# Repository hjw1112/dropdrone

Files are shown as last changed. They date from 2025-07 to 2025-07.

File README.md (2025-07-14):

# Dropdrone

This is a custom 5 inch fpv drone with modular payload system that is designed to drop stuff. (NOT for dangerous things and I will use this only in my backyard or open field in low height)

I built this because i wanted to try to move things with drone after watching some fpv drones with payload system on youtube. Also, I wanted to experience to build a fpv drone by myself not buying prebuilt stuff.

you can reference this project + copy/modify. All source files are in this repo.

### 3D model of the payload module

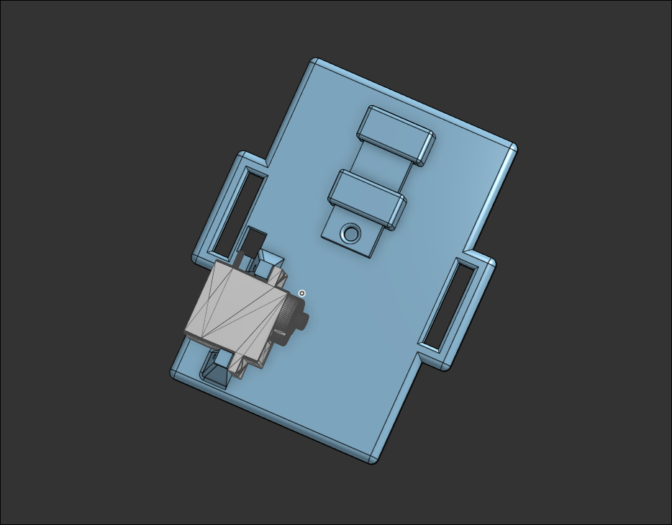
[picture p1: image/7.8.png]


### 3D model of frame

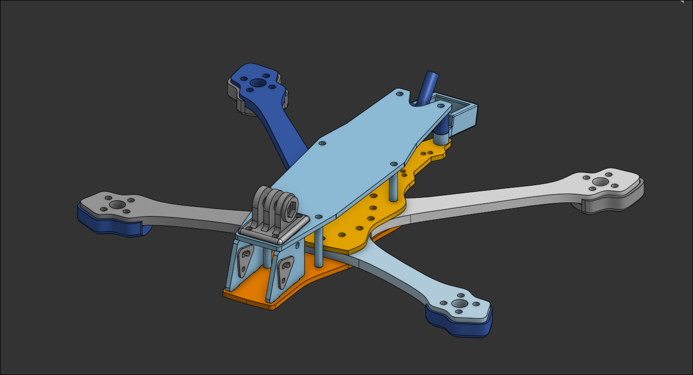
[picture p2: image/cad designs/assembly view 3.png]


### Onshape document
https://cad.onshape.com/documents/2c66b1014f978a30ab8967e0/w/781099a0622bf4fd1c422891/e/69bb565c8f452c8e317ebf30

### BOM

| Component | Price | Source | Link |
|---|---|---|---|
| GPS | $16.56  | aliexpress | [Link](https://www.aliexpress.com/item/1005008590174242.html?spm=a2g0o.cart.0.0.583438dalVaNCs&mp=1) |
| standoff 25mm, 18mm | $5.51 | aliexpress | [Link](https://www.aliexpress.com/item/10050003175594672.html?spm=a2g0o.cart.0.0.583438dalVaNCs&mp=1) |
| motor | $35.15  | aliexpress | [Link](https://www.aliexpress.com/item/1005005247800911.html?spm=a2g0o.cart.0.0.583438dalVaNCs&mp=1) |
| xt60 connector | $1.20 | aliexpress | [Link](https://www.aliexpress.com/item/1005007103483786.html?spm=a2g0o.cart.0.0.583438dalVaNCs&mp=1) |
| mipi cable for air unit| $4.15 | aliexpress | [Link](https://www.aliexpress.com/item/1005009341460132.html?spm=a2g0o.cart.0.0.583438dalVaNCs&mp=1) |
| m3 and m5 wrench | $3.54 | aliexpress | [Link](https://www.aliexpress.com/item/4000116377065.html?spm=a2g0o.cart.0.0.583438dalVaNCs&mp=1) |
| non-slip pad for battery| $3.46  | aliexpress | [Link](https://www.aliexpress.com/item/1005009871344968.html?spm=a2g0o.cart.0.0.583438dalVaNCs&mp=1) |
| m3 screw set | $8.43 | aliexpress | [Link](https://www.aliexpress.com/item/1005004526857141.html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) |
| battery strap | $2.75 | aliexpress | [Link](https://www.aliexpress.com/item/1005005249789396.html?spm=a2g0o.cart.0.0.583438dalVaNCs&mp=1) |
| lipo charger | $29.04  | aliexpress | [Link](https://www.aliexpress.com/item/1005003623858420.html?spm=a2g0o.cart.0.0.583438dalVaNCs&mp=1) |
| sg90 servo | $1.96 | aliexpress | [Link](https://www.aliexpress.com/item/1005000625304079.html?spm=a2g0o.cart.0.0.583438dalVaNCs&mp=1) |
| lipo bag | $2.98 | aliexpress | [Link](https://www.aliexpress.com/item/1005005071740139.html?spm=a2g0o.cart.0.0.583438dalVaNCs&mp=1) |
| threadlock | $1.86 | aliexpress | [Link](https://www.aliexpress.com/item/1005008289081577.html?spm=a2g0o.cart.0.0.583438dalVaNCs&mp=1) |
| fc and esc stack | $47.41  | aliexpress | [Link](https://www.aliexpress.com/item/1005007001011519.html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) |
| props x2 | $7.48 | aliexpress | [Link](https://www.aliexpress.com/item/1005007433514825.html?spm=a2g0o.cart.0.0.583438dalVaNCs&mp=1) |

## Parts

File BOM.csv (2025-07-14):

Component | Price | Source | link
GPS | $16.56 | aliexpress | https://www.aliexpress.com/item/1005008590174242.html?spm=a2g0o.cart.0.0.583438daIVaNCs&mp=1
standoff 25mm, 18mm | $5.51 | aliexpress | https://www.aliexpress.com/item/1005003175594672.html?spm=a2g0o.cart.0.0.583438daIVaNCs&mp=1 https://www.aliexpress.com/item/1005003175594672.html?spm=a2g0o.cart.0.0.583438daIVaNCs&mp=1
motor | $35.15 | aliexpress | https://www.aliexpress.com/item/1005005247800911.html?spm=a2g0o.cart.0.0.583438daIVaNCs&mp=1
xt60 connector | $1.20 | aliexpress | https://www.aliexpress.com/item/1005007103438736.html?spm=a2g0o.cart.0.0.583438daIVaNCs&mp=1
mipi cable for air unit | $4.15 | aliexpress | https://www.aliexpress.com/item/1005009431460132.html?spm=a2g0o.cart.0.0.583438daIVaNCs&mp=1
m3 and m5 wrench | $3.54 | aliexpress | https://www.aliexpress.com/item/4000017637065.html?spm=a2g0o.cart.0.0.583438daIVaNCs&mp=1
non-slip pad for battery | $3.86 | aliexpress | https://www.aliexpress.com/item/1005006987134496.html?spm=a2g0o.cart.0.0.583438daIVaNCs&mp=1
m3 screw set | $8.43 | aliexpress | https://www.aliexpress.com/item/1005004526853714.html?mp=1
battery strap | $2.75 | aliexpress | https://www.aliexpress.com/item/1005007125752501.html?spm=a2g0o.cart.0.0.583438daIVaNCs&mp=1
lipo charger | $29.04 | aliexpress | https://www.aliexpress.com/item/1005005947893976.html?spm=a2g0o.cart.0.0.583438daIVaNCs&mp=1
sg90 servo | $1.96 | aliexpress | https://www.aliexpress.com/item/1005006283358420.html?spm=a2g0o.cart.0.0.583438daIVaNCs&mp=1
lipo bag | $2.98 | aliexpress | https://www.aliexpress.com/item/1005007625304079.html?spm=a2g0o.cart.0.0.583438daIVaNCs&mp=1
threadlock | $1.86 | aliexpress | https://www.aliexpress.com/item/1005008298085771.html?spm=a2g0o.cart.0.0.583438daIVaNCs&mp=1
fc and esc stack | $47.41 | aliexpress | https://www.aliexpress.com/item/1005007050011519.html?spm=a2g0o.cart.0.0.583438daIVaNCs&mp=1
props x2 | $7.48 | aliexpress | https://www.aliexpress.com/item/1005007433514825.html?mp=1
discount | $22.11
total | $149.77
I'm buying these
dji o4 air unit | $110.00 | local store
lipo battery | $50.00 | local store

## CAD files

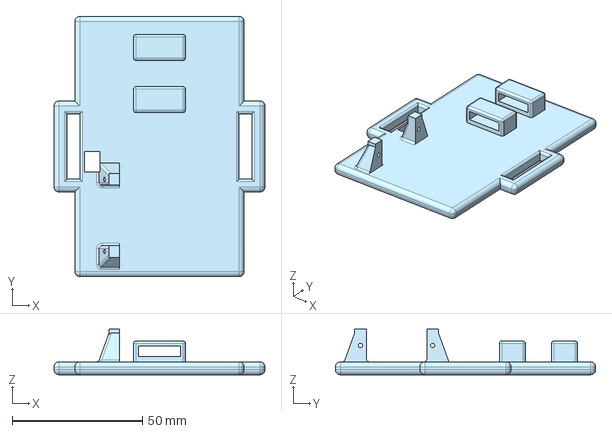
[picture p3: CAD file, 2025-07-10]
CAD/drop system/main body.step
81.0 x 100.0 x 17.5 mm

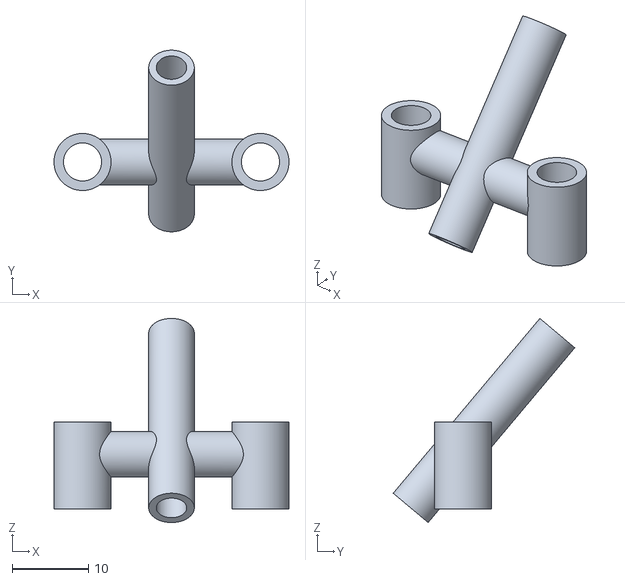
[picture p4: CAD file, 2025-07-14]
CAD/frame/antenna mount.stl
30.9 x 23.9 x 26.8

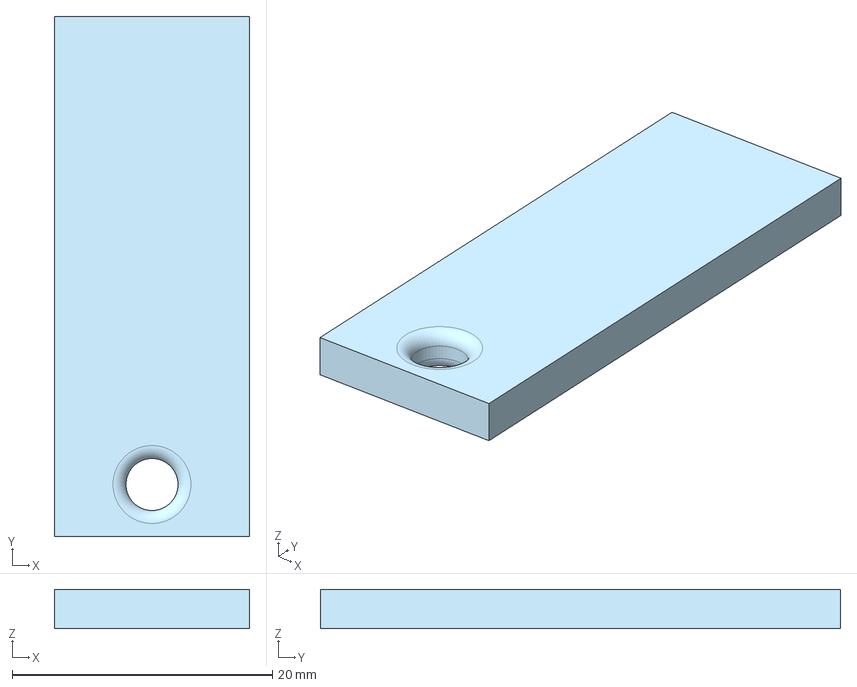
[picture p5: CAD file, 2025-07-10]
CAD/drop system/stick part.step
15.0 x 40.0 x 3.00 mm

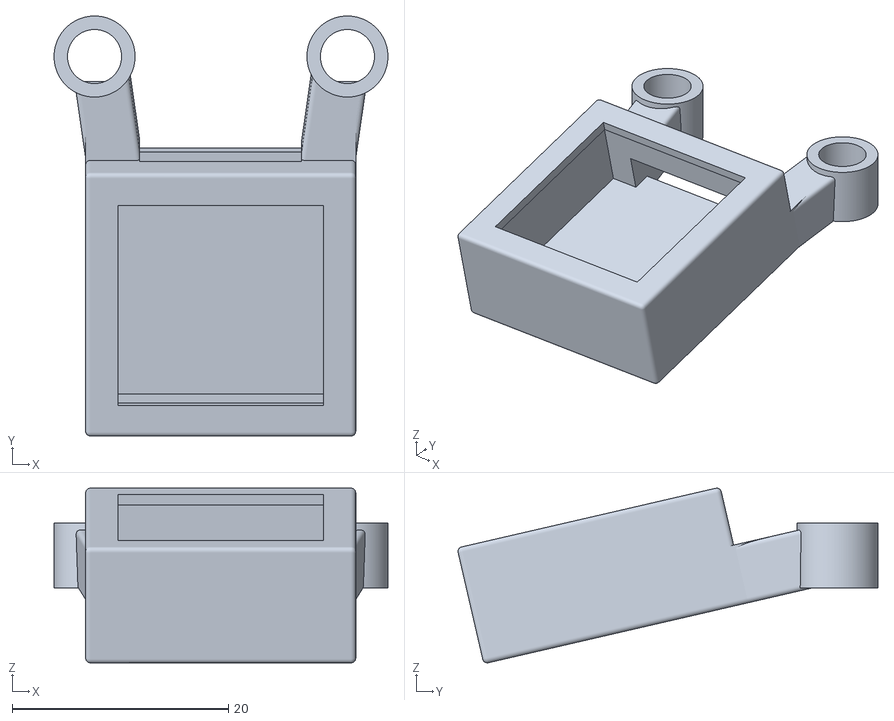
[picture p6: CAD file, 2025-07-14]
CAD/frame/gps mount.stl
30.9 x 38.9 x 16.2

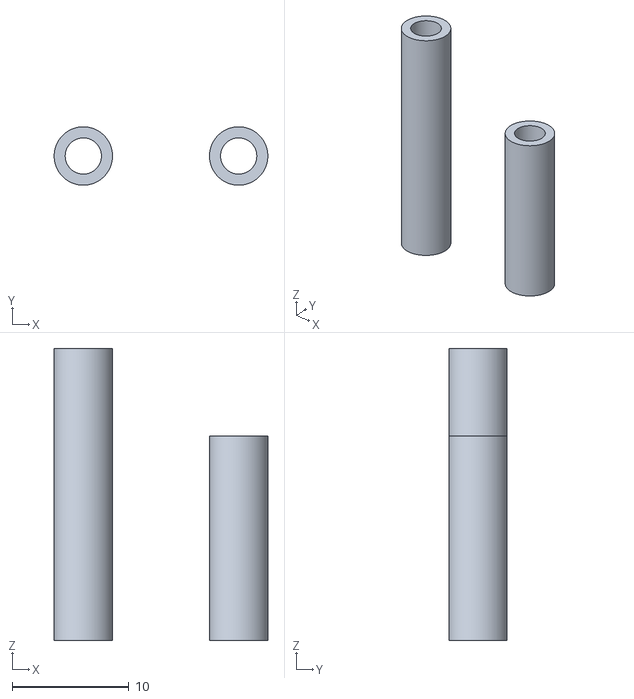
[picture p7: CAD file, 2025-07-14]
CAD/frame/standoffs.stl
18.3 x 5.00 x 25.0

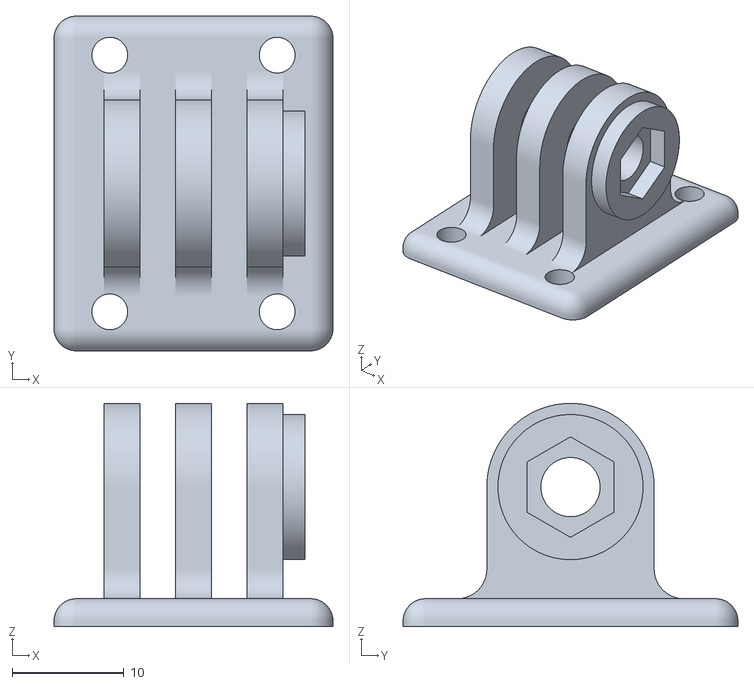
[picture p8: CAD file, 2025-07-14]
CAD/frame/gopro mount.stl
25.0 x 30.0 x 20.0

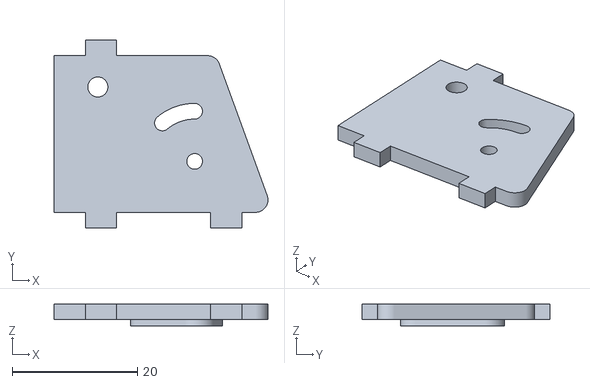
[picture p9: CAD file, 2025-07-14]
CAD/frame/side plate and cam mount.stl
34.1 x 30.0 x 3.50

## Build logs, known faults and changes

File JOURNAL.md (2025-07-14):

---
title: "Dropdrone"
author: "hjw1112"
description: "A custom built 5 inch fpv drone that can carry stuff"
created_at: "2025-07-04"
---

### onshape document
https://cad.onshape.com/documents/2c66b1014f978a30ab8967e0/w/781099a0622bf4fd1c422891/e/69bb565c8f452c8e317ebf30

### **total hours: 40.5h**

# July 4th: Start!

I did research about components and sourced some components from aliexpress. I will use dji O4 air unit, xing 2207 motor, SG90 servo, 5 inch frame, M100 GPS, and Speedybee F450 stack. It took a while because components are expensive and i was trying to reduce cost as much as possible.

Also, I started to working on 3d modeling of servo payload system. I saw a video on youtube (https://www.youtube.com/shorts/8GbMEWLD8KA) which is simple payload system on fpv drone. I will benchmark this and make similar one. But I'm going to make it better and more refined because one in the video is made out of some random metal part and zip tie. I will use 3d printed part and possibly a metal part for stronger holder for smaller thickness.

I started looking and planning 3d model by looking at carbon fiber frame that i chose on aliexpress. I think i will mount servo on the backside of the drone and put locking system at the center of the drone for stability.

**Total time spent: 6h**

# July 5th: Component changes and 3d modeling start

I did more research and a lot of searching on aliexpress for cheaper materials. I found cheaper SG90 servo so i replaced it. and i also found similar frame for better price so i replaced it too. it doesn't include 3d printed parts but i can design and print them myself ig. I replaced speedybee stack to unknown branded but cheaper stack.

I restarted to plan 3d model again cuz i changed frame and I will use holes for holding top and bottom part together to hold 3d printed servo mount(I will use longer screw) and put servo on the mount. 

**Total time spent: 5h**

# July 6th: more component changes and 3d modeling again

I'm currently trying to reduce cost and it is so hard :(( Its 383$ now including dji O4 air unit lite. I'm trying to fit everything under 150$ without air unit and battery. I changed motor to sunfun 2207 1750kv which is cheaper.

I restarted 3d modeling AGAIN because i wanted the payload system be removable and modular since flight time can be extended if payload system is removable.
I'm planning to use fpv battery strap to hold 3d printed payload system onto the frame.

Currently, I made hole for wire and mount for servo motor. I'm planning to add strap hole on the left and right side.

### Current CAD

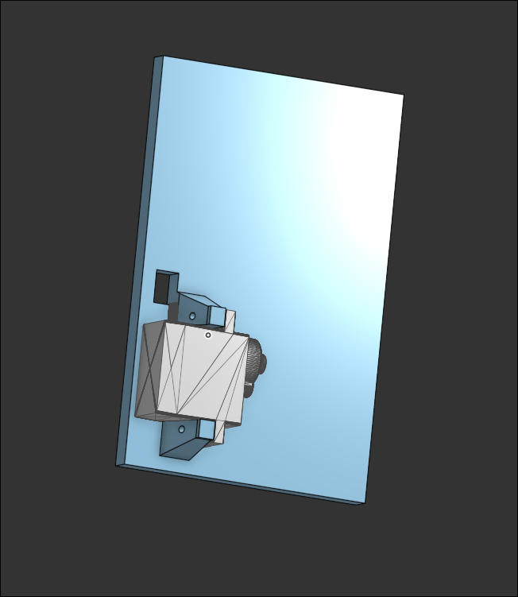
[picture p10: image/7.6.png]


**Total time spent: 5h**

# July 8th: Finished CAD!!

I finished CAD part. I added holes for strap and lock part. idk if it will work perfectly. So i'm going to fix it if it doesnt work when i get the servo. the hole will work as pivot and i will use metal strip to connect motor and the hole.



### some sketches that i draw during modeling

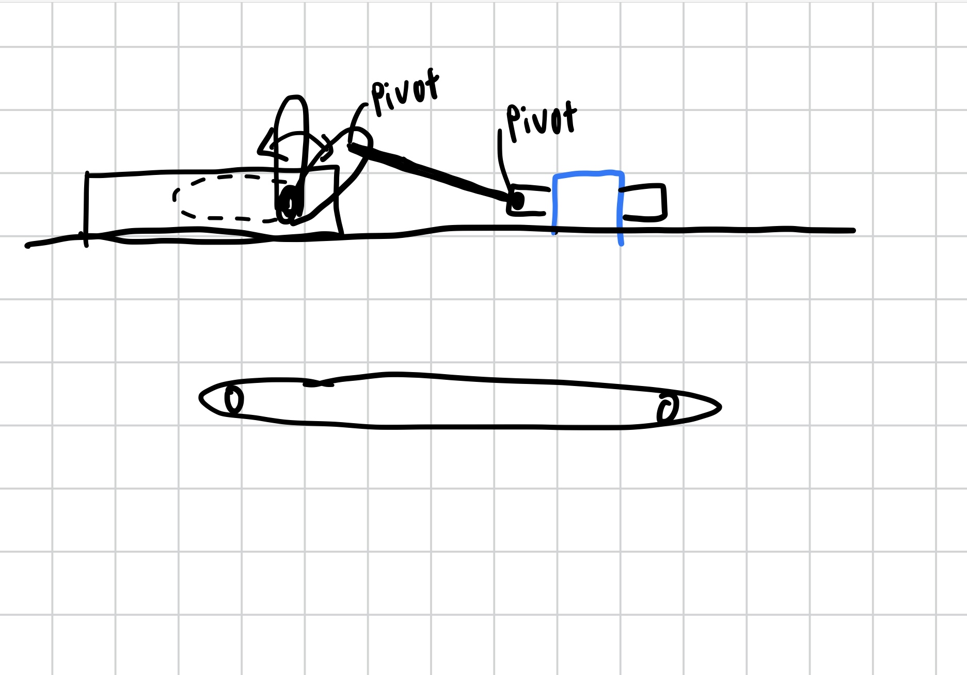
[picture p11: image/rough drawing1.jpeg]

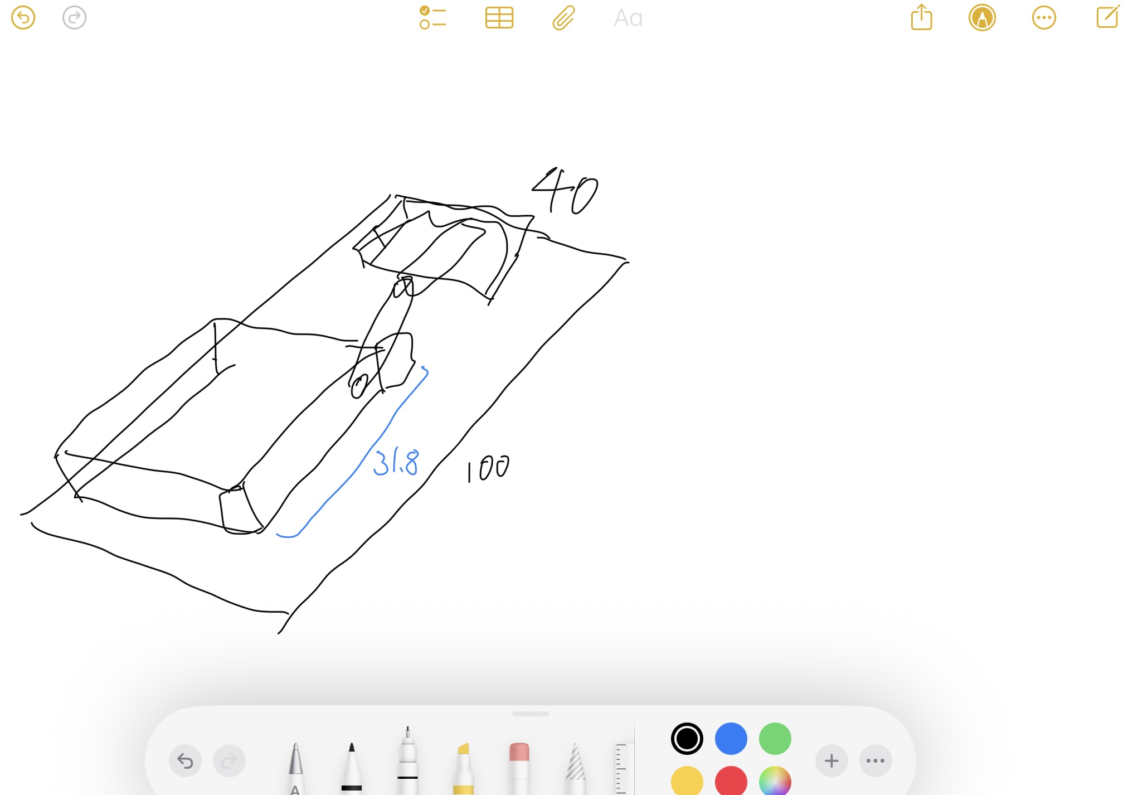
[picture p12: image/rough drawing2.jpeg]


**Total time spent: 2h**

# July 10th: Finished!! (not really)

Today. I worked on reducing cost again. I replaced some parts with cheaper alternative and applied sale coupon :) So it is under 150$ without air unit and battery

Also, I wrote BOM csv for submission.

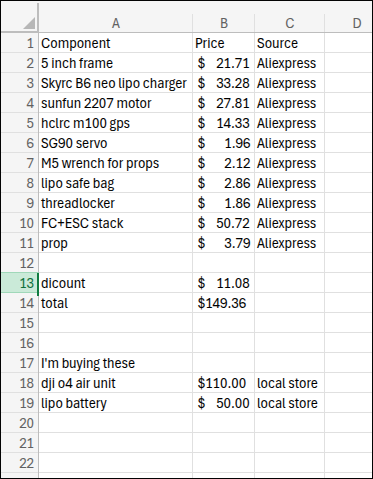
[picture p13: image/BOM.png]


**Total time spent: 3h**

# July 11th: CHANGES!!!

I found out that my project is a bit simple so i decided to design frame by myself. I was trying to do so when i was planning before i start and i 3d printed some test parts to see if it works. But it was too weak and bent so easily to be used for fpv frame. So i decided to use premade carbon fiber frame.

However, I found about cf cnc and it wasn't that expensive like i thought so i decided to use it. 

I started designing fpv frame. It was kinda confusing because idk how to shape the parts. So i tried tracing frame photo on internet but tracing wasn't perfect and it seems to be more complicated than designing from scratch. So i decided to make one from scratch but using photo as reference.

I designed arm and + shaped support first. and this is the result. I was worried about thin points so i edited quite a lot and finally got right design :)

I made some reference sketch like center line and holes so I can mirror sketches to make other side and make hole for screws on other parts easily.

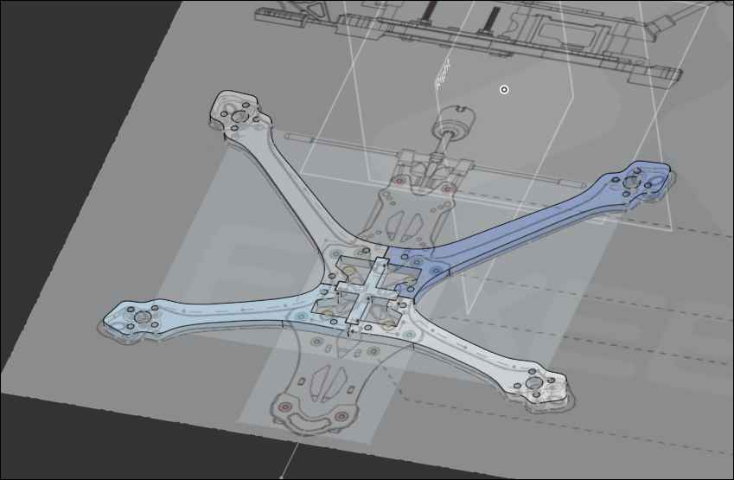
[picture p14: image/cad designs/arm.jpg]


Next, I designed bottom plates. I seperated them into 2 pieces as most fpv frame does. I traced the photo a bit but changed most of the parts to make the holes that i made on arm work.

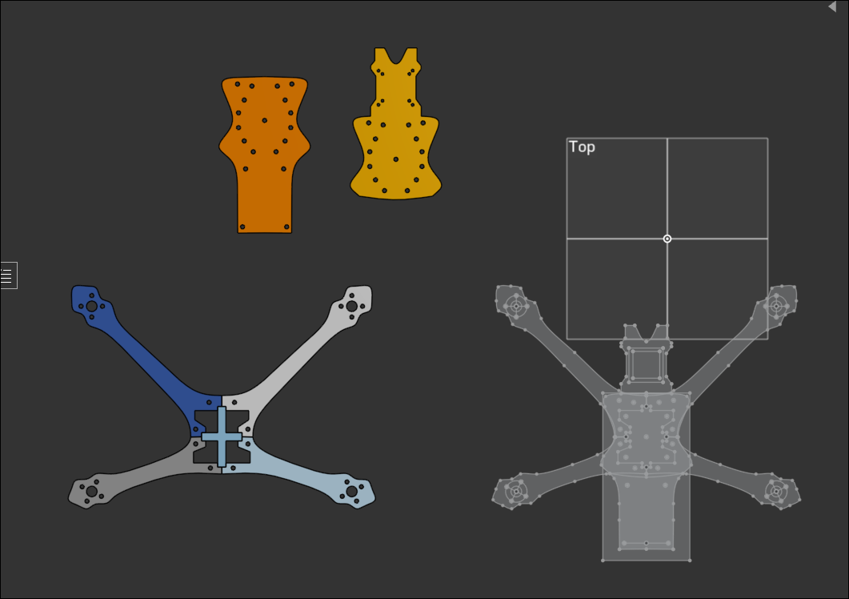
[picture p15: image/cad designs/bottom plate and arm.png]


**Total time spent: 8h**

# July 12th: More CADD

I printed the parts that i designed yesterday and it was very nice. the arm and + shaped support fits very well and holes are alligned nicely. But the pointy part of plate was making the frame too big so i reduced its size. 

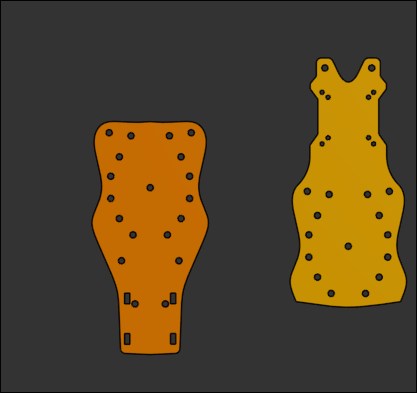
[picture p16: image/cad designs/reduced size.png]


Also, I made side plate for mounting camera(+holes on plate). It was quite confusing process because idk how to make it and also most of frames use cnc aluminium side plate with threaded hole. but i cannot use cnc so i used some knobs to hold it in place and used top plate and bottom plate to hold it. and i made tpu dampner/connector for camera too. 

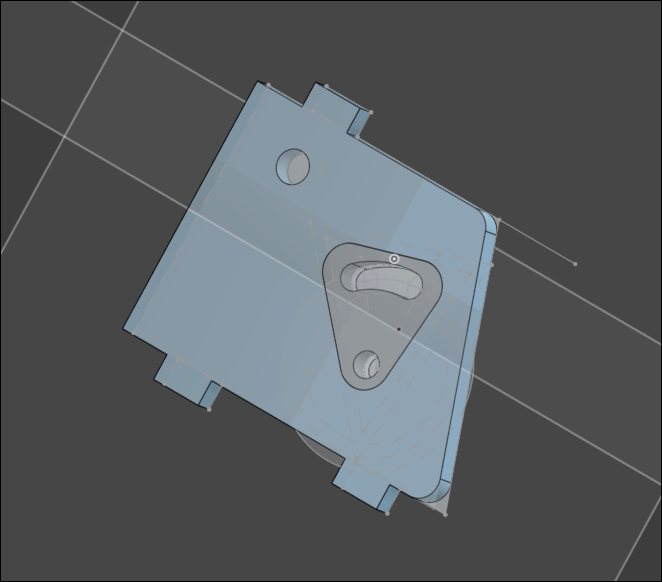
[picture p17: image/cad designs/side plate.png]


lastly, I designed top plate and addeddummy standoffs to see if it looks good. here's overall assembly view for now.

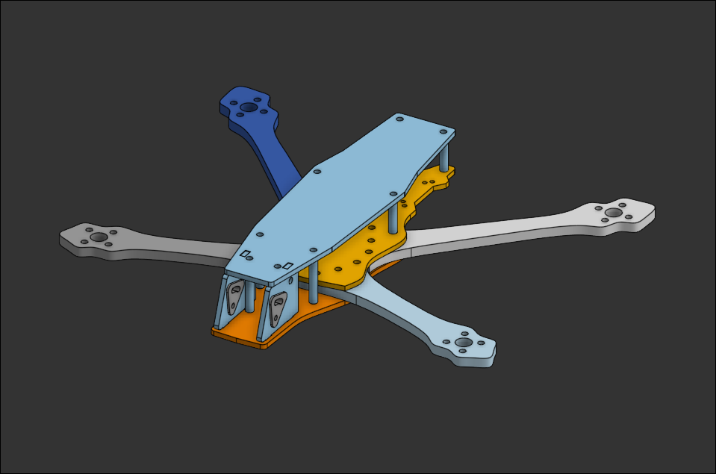
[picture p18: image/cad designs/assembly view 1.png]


I'm quite happy how it turned out :))

Now. i'm going to make some holed on the plates and test print the parts to see if it works well as i designed them. Then, i think i will design some replacable parts like landing gear, antenna holder, and gopro mount.

**Total time spent: 6h**

# July 13th: More CADD

First, I chose to use 3d printed frame because it was quite firm with 100% infill. and I will also use 3d printed standoffs with heatset insert because there is no point of using metal standoff when whole frame is plastic.

I designed gopro mount, landing gear, and antenna+gps mount today. Also, I sourced more materials like battery strap, non-slip pads for battery, mipi cable extension for cam mounting, heatset insert, and etc. It wasn't that hard process because it wasn't confusing and complex like frame design. I will edit some part after testing out when i get the components.

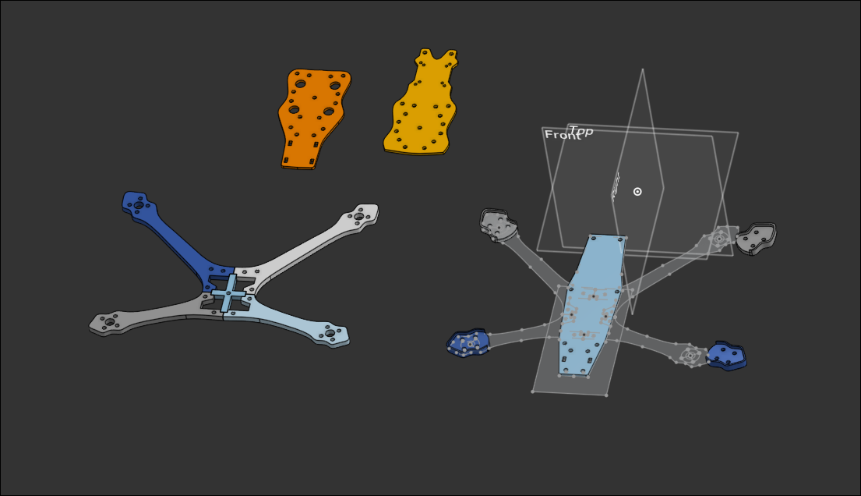
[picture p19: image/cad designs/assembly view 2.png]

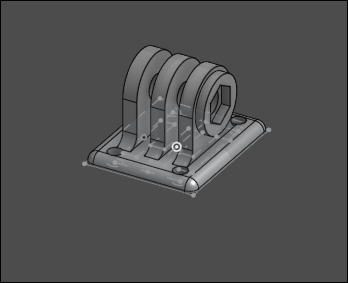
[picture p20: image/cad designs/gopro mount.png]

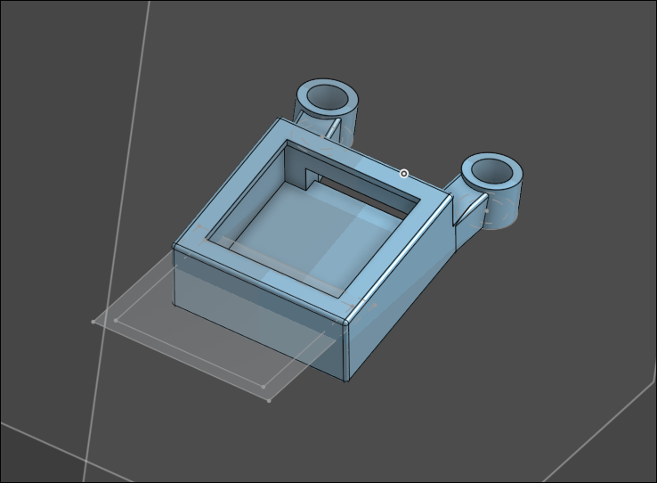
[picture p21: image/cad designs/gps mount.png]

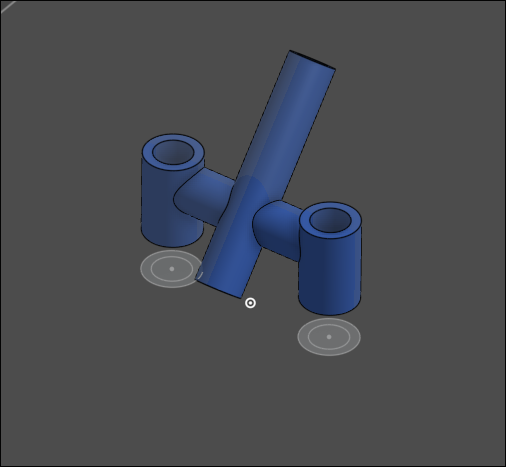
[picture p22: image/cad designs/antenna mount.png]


**Total time spent: 5h**

# July 13th: FINISHHHHH

I edited BOM since i had some changes and I chose to use metal standoffs because i think it will be too weak and top plate could fall off from frame if i use 3d printed ones.

### One last photo with everything together



**Total time spent: 0.5h**

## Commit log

2025-07-10 added bom and cad
    [BOM.csv, main body.step, stick part.step]
2025-07-14 7/13 + cad files
    [gopro mount.stl, side plate and cam mount.stl, standoffs.stl]
2025-07-14 added gps and antenna mount
    [antenna mount.stl, gps mount.stl]
2025-07-14 organized dir/updated bom/added 7/14
    [BOM.csv, antenna mount.stl, gopro mount.stl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]
2025-07-14 added assembly view 3 screenshot
